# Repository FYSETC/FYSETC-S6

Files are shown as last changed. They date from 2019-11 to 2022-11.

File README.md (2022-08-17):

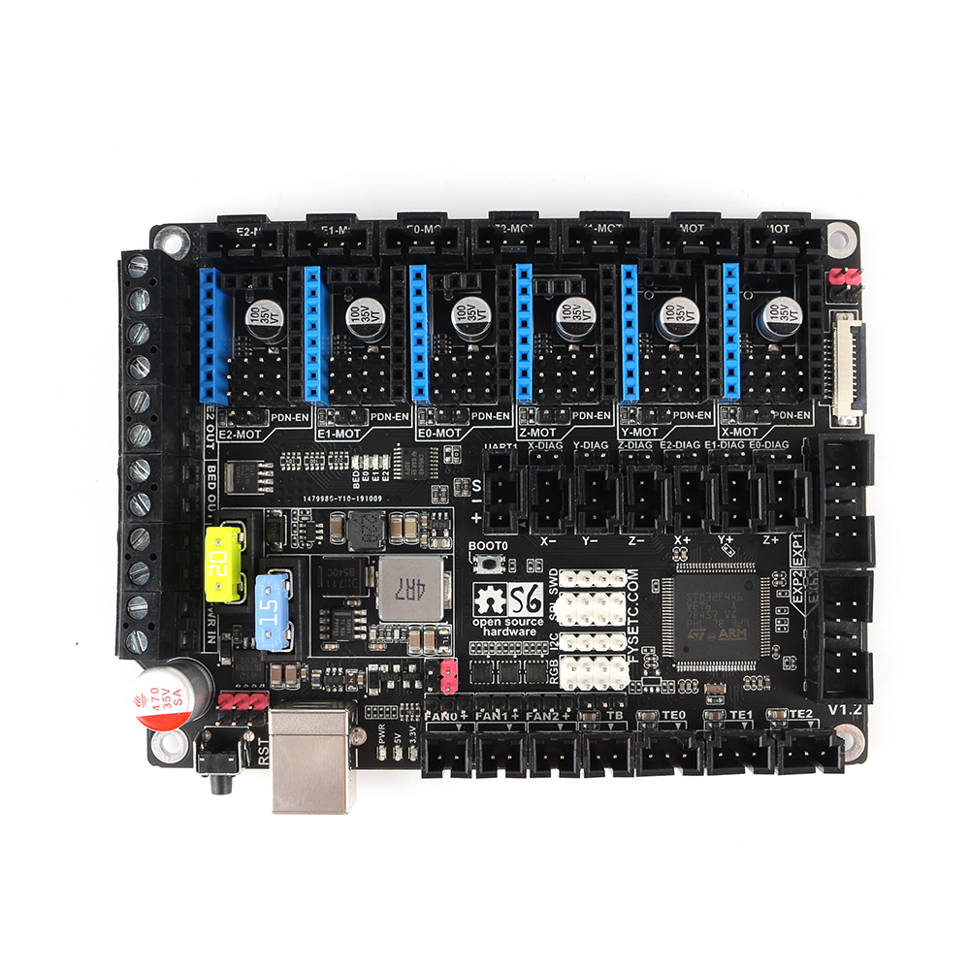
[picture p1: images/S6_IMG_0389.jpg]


The S6 is based on the STM32F446 32bit mcu, like the F6, has six drive sockets and supports the full range of TMC drives. We have fully extended the resources of the MCU so that you can maximize its power. We considered the possible use scenarios of 3D printers and designed a series of extended applications, such as anti-reverse circuit, 12V power supply, thermocouple support, 24V sensor support and so on.

## 1. Features

- Compact size: 117mm x 87mm，Same as F6
- Based on STM32F446 180Mhz，all IOs can withstand 5V voltage
- 6 TMC stepper drivers support, no need wire Uart/SPI
- Improved TMC jumper settings ，simpler and easier to understand
- Main power reverse protection circuit，safer
- 28V input max，12V@5A，5V@2ADC-DC circuit，3.3V@0.6A LDO
- Two car fuses for hot bed input and main power input
- Limit switch socket 24V/5V/3.3V optional, ready for more other equipment, such as -inductive sensor, BL-Touch
- XH connector and MX connector are optional
- 10x PWM capable power mosfet outputs (1 for HotBed, 3 for Heat-End, 3 for fans, 3 for RGB LED strip) 
- 3pin temperature header, you can use thermistor or thermocouple (requires AD597 module)
- 3 ways PWM fans ，2 ways RGB led ，12V & 24V optional
- Easy DISPLAY + SD-CARD connector:

  - RepRapDiscount SmartController compatible pin header on board
  - 10P FPC for Serial Touch display
  - 2X4 PinHeader Out for SD Card moudle 
  - EXP1 & EXP2 have more multiplexing functions, such as USART, I2C, CAN
- SD card & USB upload support
- S6 v2.1: **Add more protection** **(current** **limit resistor, VMOT fuse)**

## 2. Application

---

- 3D printer 

- CNC Device

- Other similar machines

## 3. Hardware 

### 3.1 Reasources

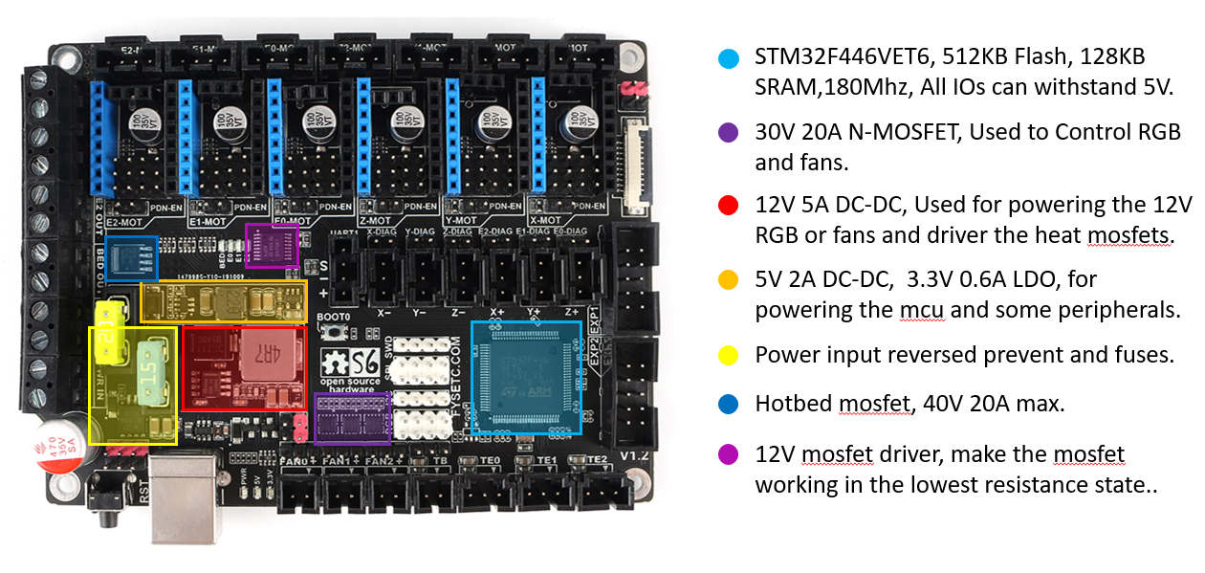
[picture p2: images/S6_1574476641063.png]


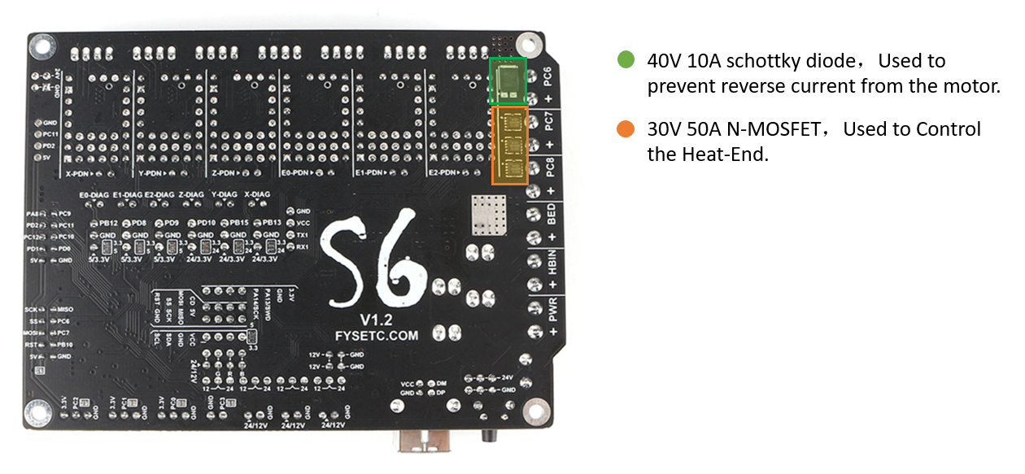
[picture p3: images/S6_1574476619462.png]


| Board Name | S6 | F6 |
| --- | --- | --- |
| License | GPL V2.0 | GPL V2.0 |
| Latest Version | V1.2 | V1.4 |
| Extruders | 3 Max | 3 Max |
| Fixed Fans | 5 Max | 5 Max |
| Controlled Fans | 3 Max | 3 Max |
| Heaters | 3 Max | 3 Max |
| Endstops | 6 Max | 6 Max |
| Temp sens | 4 Max | 4 Max |
| SPI | 2 Max | 1 |
| I2C | 3 Max | 1 |
| ISP | -- | 1 |
| Serial port chip | -- | CH340 |
| CPU | STM32F446VET6 | Atmega2560 |
| CPU Speed ( MHz ) | 180Mhz | 16 Mhz |
| Stepper driver | 6 Max | 6 Max |
| Stepper driver  Type | All StepStick compatible modules | All StepStick compatible modules |
| Input | Main PWR：12-24V 15A Max；BED IN：12-24V 20A Max | Main PWR：12-24V 10A Max；BED IN：12-24V 15A Max |
| Output | BED OUT：20A Max ；Heater Out：5A Max | BED OUT：15A Max ；Heater Out：5A Max |

### 3.2 Jumpers 

---

**Just like the F6 V1.4, the two Z-motor sockets are changed from parallel to series. If you only use one of the sockets, the other must be connected with a jumper cap, otherwise a Z-axis motor will not work.**

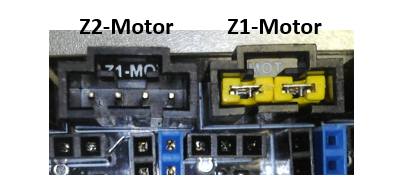
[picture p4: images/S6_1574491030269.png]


#### 3.2.1 Stepper drivers

In order to support as many different drivers as possible, S6 sets a lot of jumper positions. Different drive modules require different jumpers. As shown in the schematic diagram, there are 2 sets of jumpers in the drive section: JP1 and  JP6. 

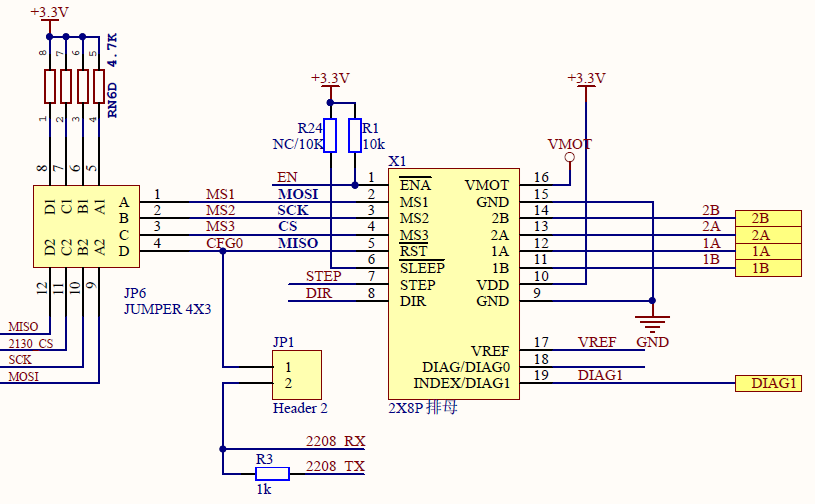
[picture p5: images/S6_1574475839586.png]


In order to give you a better understanding of how to use jumpers for different drivers, I have further illustrated the driver socket. The basic definition of the driver pins is the same, the difference lies in the four places of JP6-1, JP6-2, JP6-3 and JP6-4. You can see their role from the schematic.

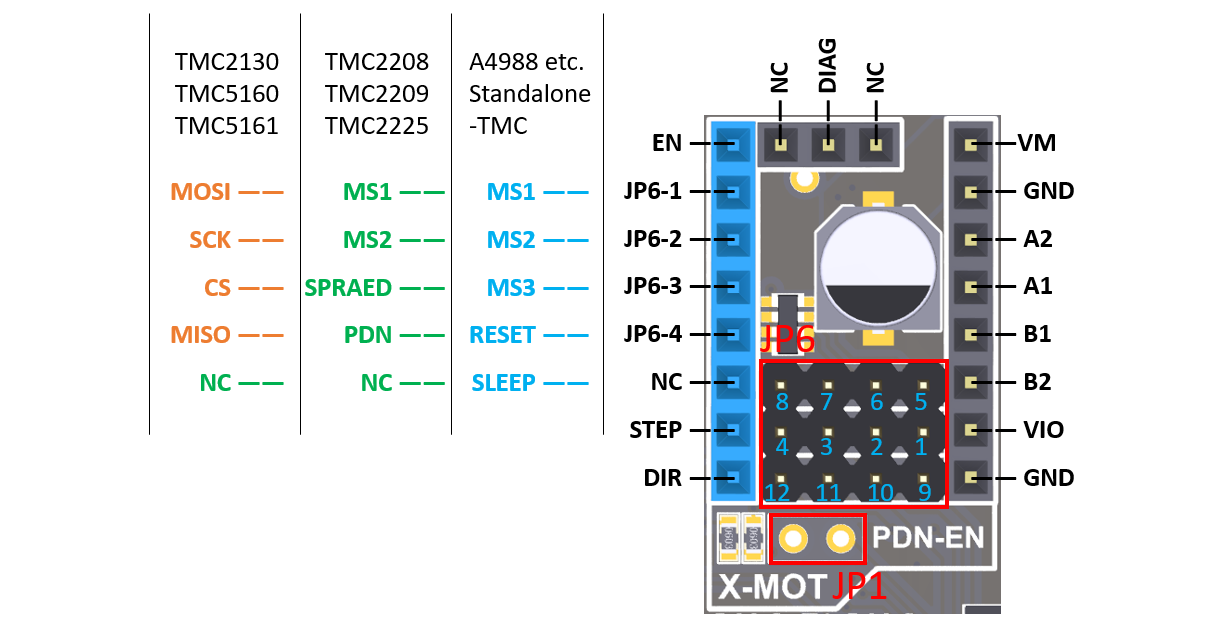
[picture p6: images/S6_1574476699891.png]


##### A4988 jumper config

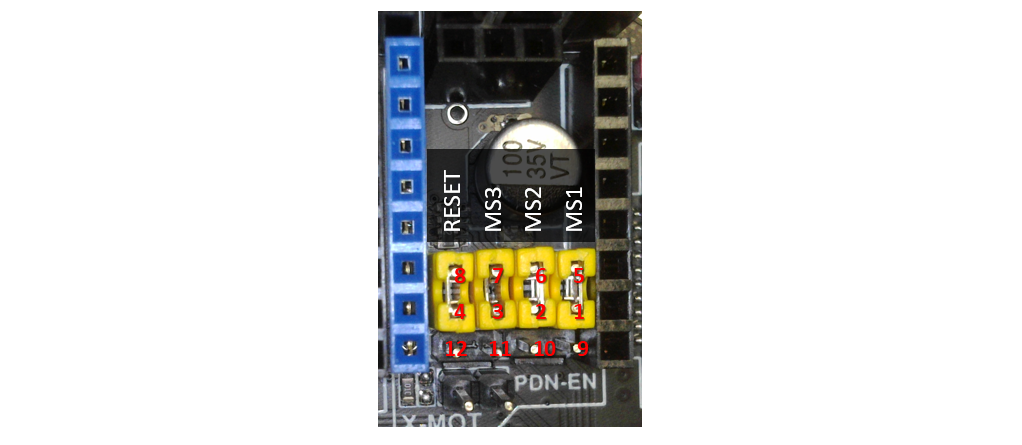
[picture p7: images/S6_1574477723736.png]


- For A4988, A4988 similar, TMC2100 and TMC standalone Mode,  You need jumper JP6 (1234-5678) to config the micro-steps, and some TMC features.
- When you connect the jumper cap, this pin is high. When you are not connected, it is the level state of the module itself. This is different from F6, which can be either high or low.
- For details, please refer to the corresponding driver description.

##### UART mode config

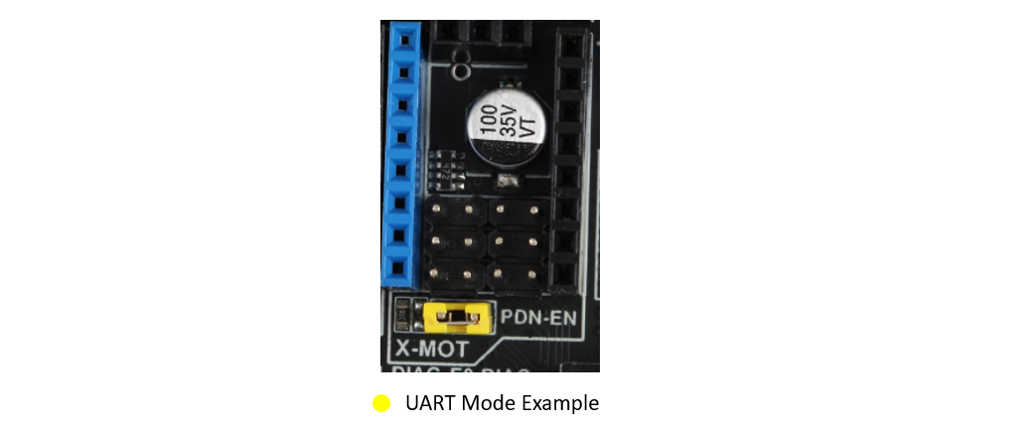
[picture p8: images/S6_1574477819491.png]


- For TMC2208/2225/2209. You just need one jumper to close the JP1, Then the UART mode will enabled.
- You can config all the feature of  the TMC chip via UART, so you can leave all the other jumpers empty.
- Even for 2209, We give 2 lines UART interface to every driver, so no need config the address by MS1/MS2.

###### TMC2209 wiring

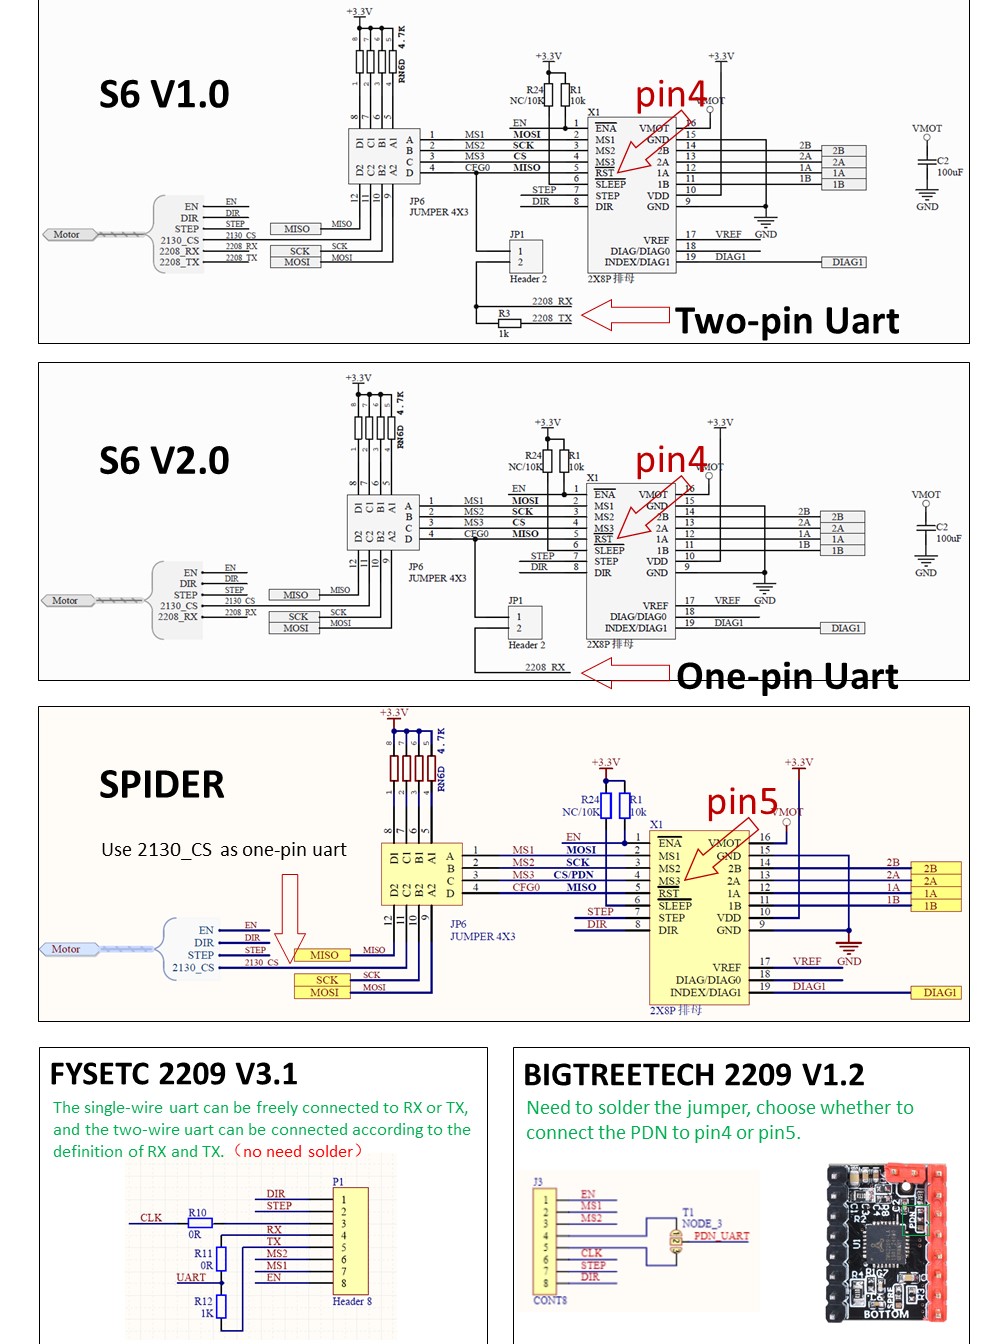
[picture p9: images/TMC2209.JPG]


##### SPI mode config

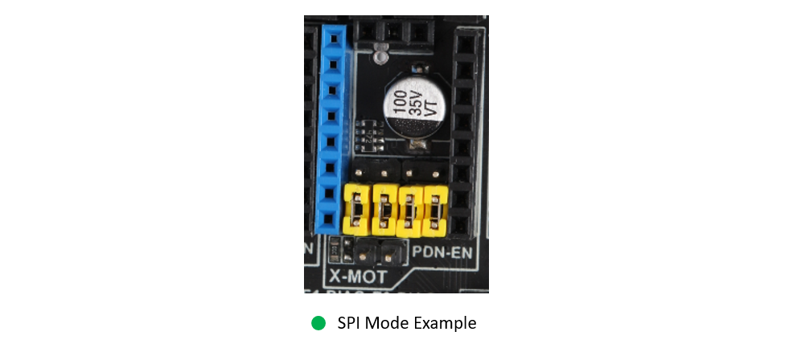
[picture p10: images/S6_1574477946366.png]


- For TMC2130/5160/5161. You need 4 jumpers to close the JP6, Then the SPI mode will enabled.

#### 3.2.2 12V/24V jumpers

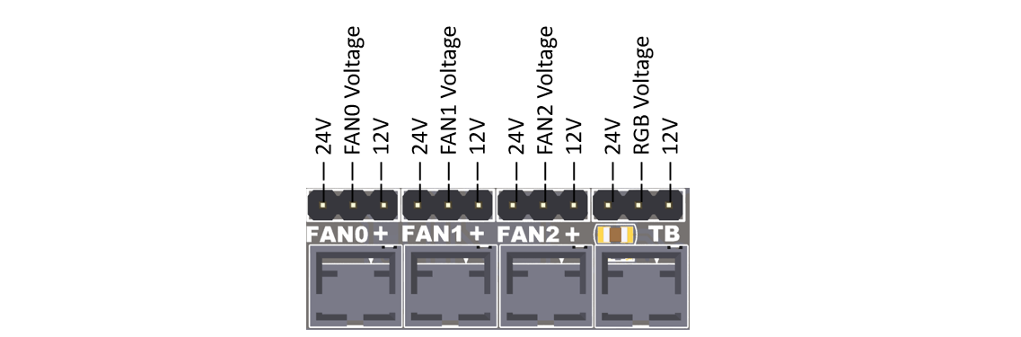
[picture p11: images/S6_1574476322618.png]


- S6 have 12V onboard, Fan and RGB jumpers can refer to this picture and the silk screen at the bottom of the board.
- The input power supply voltage should EXCEED 15v ,if not, the output voltage of 12V DCDC circuit will lower than 12v
- Never let the 12V current exceed 5A, otherwise it will burn out the 12V DCDC circuit.
- If you use an input above 18V, you will get a satisfactory 12V output, otherwise the output may be less than 12V.

#### 3.2.3 DIAG jumpers

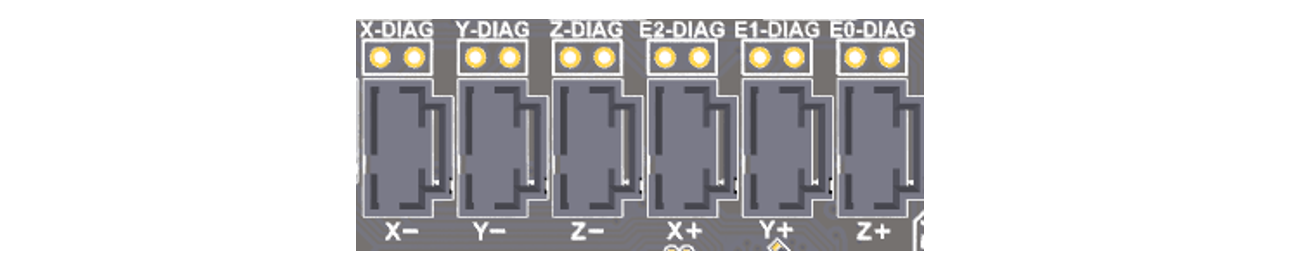
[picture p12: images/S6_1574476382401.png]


- If you use a TMC driver with sensor-less homing(2130/2209/5160/5161), you can connect these jumpers so that the MCU can get the DIAG signal through the corresponding end-stop pin to achieve sensor-less.
- After connect the jumper, remember define the DIAG pins in the firmware and enable the feature.

#### 3.2.4 Bottom jumpers

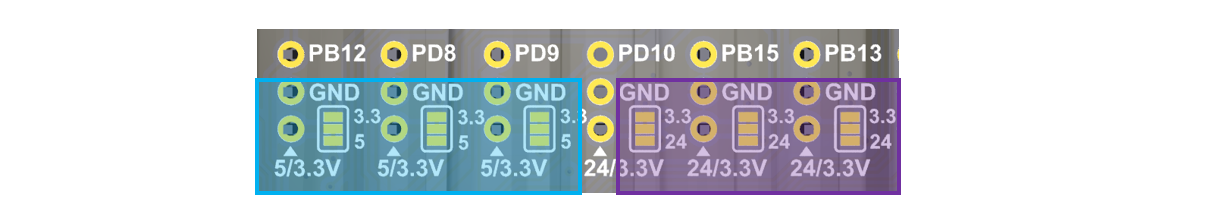
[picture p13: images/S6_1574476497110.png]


- X+ / Y+ / Z+ , You can choose 5V or 3.3V, For X+ & Y+, the default is 3.3V. For Z+, The default is 5V, You can connect BLtouch here.

- X- / Y- / Z- , You can choose 24V or 3.3V, the default is 3.3V. You can switch to 24V, if you want to use some inductive or capacitive sensors.

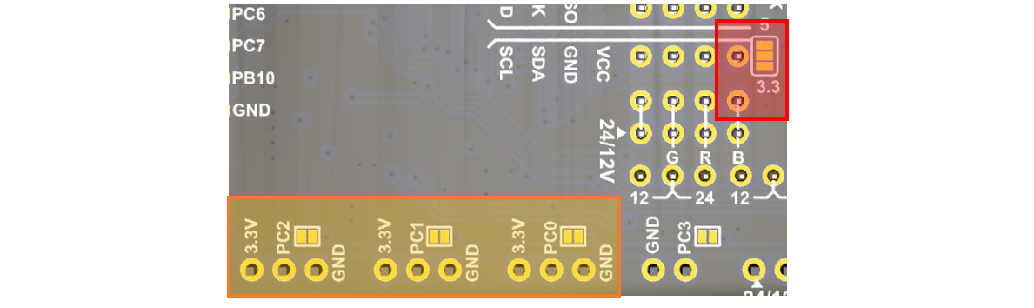
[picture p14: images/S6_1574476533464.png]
  

- I2C pins, You can choose 5V or 3.3V, the default is 3.3V. 

- For TE0-TE2, You can cut the jumper if you want use a thermocouple temperature measurement through AD597.

#### 3.2.5 Jumper for 5V

S6 **V2.0** version adds 5V selection jumper. You can choose 5V from USB or DC circuit. 

Know issue: With 5V USB jumper selected, 24V applied, USB cable disconnected, the heater FETs will turn on.  So we recommend you to choose 5v from DC5V.

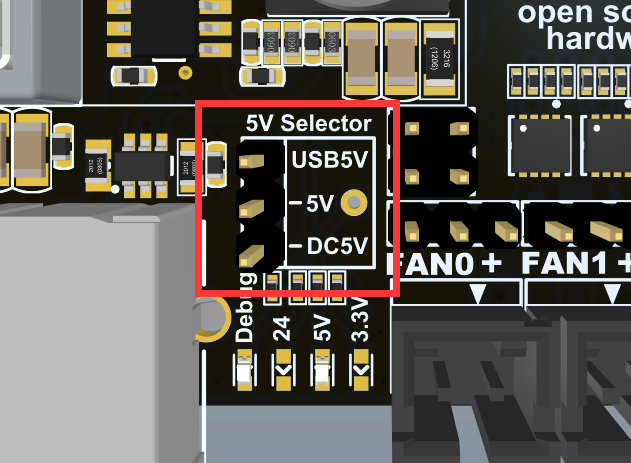
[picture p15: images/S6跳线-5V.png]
S6跳线-5V


#### 3.2.6 Jumper for Boot0

In S6 V2.0, the BOOT0 button is replaced by a jumper.

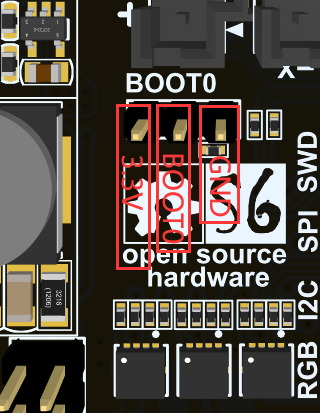
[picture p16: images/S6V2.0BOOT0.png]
S6V2.0BOOT0


### 3.3 Pin Definition

All the pins we have marked on the back of the board, if you need to, you can confirm the board in reverse or check the sch.

Thanks to the power of the STM32, each pin has multiple functions, I will identify it for your reference as much as possible. For further information, please refer to the STM32F446 datasheet, which I have placed on our [S6 GitHub](https://github.com/FYSETC/FYSETC-S6/blob/master/datasheet/stm32f446ve.pdf)

#### 3.3.1 EXP1&EXP2

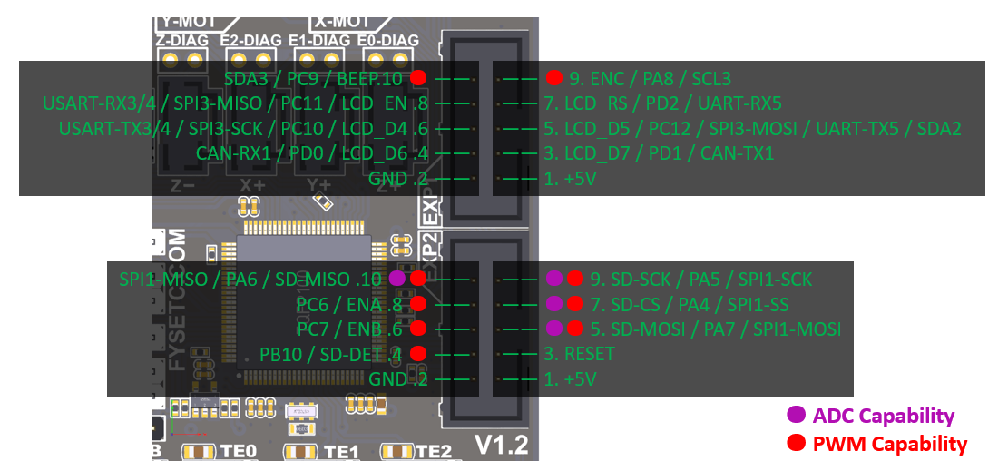
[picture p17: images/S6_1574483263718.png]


#### 3.3.2 Eedstops and UART1 Pins

The UART socket next to the limit switch can be used to connect serial devices such as the wifi module, or to update the firmware through the serial port.

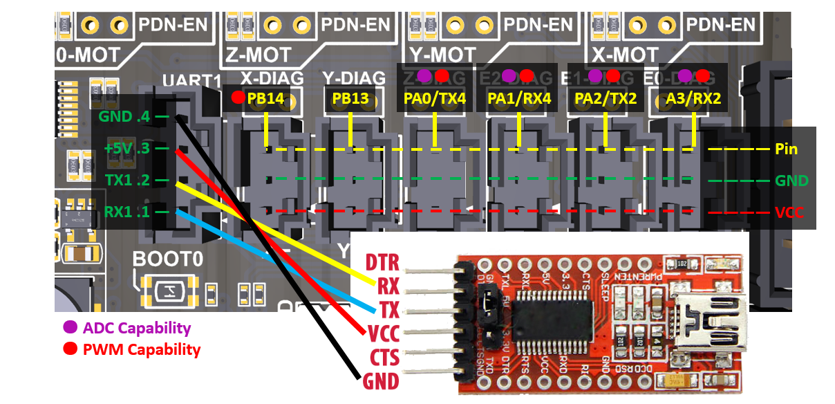
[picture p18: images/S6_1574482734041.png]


#### 3.3.3 BL-touch Wiring Example

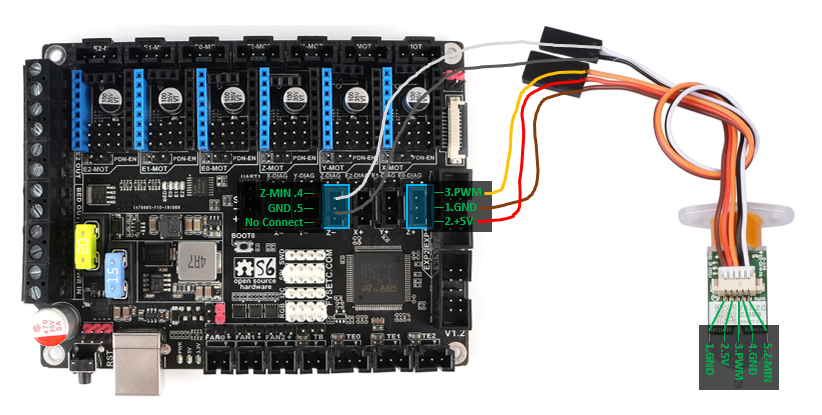
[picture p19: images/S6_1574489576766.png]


#### 3.3.4 Reuse RGB ports for FAN

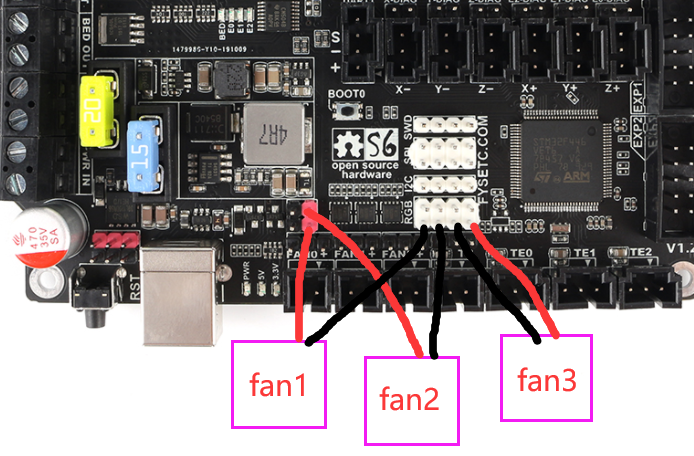
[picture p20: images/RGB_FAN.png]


## 4. Firmware

---

### 4.1 Marlin

#### 4.1.1 Download Vscode + platformio

To compile the firmware , you need to install Visual Studio Code and the platformio pulg-in. More details of Marlin build, check [here](https://marlinfw.org/docs/basics/auto_build_marlin.html).

#### 4.1.2 Download firmware

##### S6 v1.2

The firmware is in the `firmware` folder in this repository, and if you want to know what we have changed , we recommend to use git to get the code .

If you want to have latest feature of Marlin , we recommend to use latest [Marlin bugfix-2.0.x branch](https://github.com/MarlinFirmware/Marlin/tree/bugfix-2.0.x) , after downloading ,you need to enable following define in ```configuration.h``` file  

```#define MOTHERBOARD BOARD_FYSETC_S6```

then change the ```default_envs``` variant in ```platformio.ini``` file

```default_envs = FYSETC_S6_8000``` (Recommended. boot address is `0x8000`. You need to flash the bootloader([github](https://github.com/FYSETC/FYSETC-S6/blob/main/bootloader/Bootloader-FYSETC_S6.hex) [gitee](https://gitee.com/fysetc-mirrors/FYSETC-S6/blob/main/bootloader/Bootloader-FYSETC_S6.hex)) first, check the `README` on the link)

```default_envs = FYSETC_S6``` (For old bootloader,boot address is `0x10000`, you need to flash this bootloader([github](https://github.com/FYSETC/FYSETC-S6/blob/main/bootloader/Bootloader-FYSETC_S6_10000.hex) [gitee](https://gitee.com/fysetc-mirrors/FYSETC-S6/blob/main/bootloader/Bootloader-FYSETC_S6_10000.hex)) first , check the `README` on the link)

**Note: The bootloader boot address have been change to `0x8000` since 2021/06/23, you can check bootloader details [here](https://github.com/FYSETC/FYSETC-S6/tree/main/bootloader), and you can check the Marlin PR [here](https://github.com/MarlinFirmware/Marlin/pull/22207).**

##### S6 v2.x

The firmware is in the `firmware` folder in this repository , you can also get the firmware from latest [Marlin bugfix-2.0.x branch](https://github.com/MarlinFirmware/Marlin/tree/bugfix-2.0.x). You need to enable following define in ```configuration.h``` file  

```#define MOTHERBOARD BOARD_FYSETC_S6_V2_0```

then change the ```default_envs``` variant in ```platformio.ini``` file

```default_envs = FYSETC_S6_8000``` (Recommended. boot address is `0x8000`. You need to flash the bootloader([github](https://github.com/FYSETC/FYSETC-S6/blob/main/bootloader/Bootloader-FYSETC_S6.hex) [gitee](https://gitee.com/fysetc-mirrors/FYSETC-S6/blob/main/bootloader/Bootloader-FYSETC_S6.hex)) first, check the `README` on the link)

```default_envs = FYSETC_S6``` (For old bootloader,boot address is `0x10000`, you need to flash this bootloader([github](https://github.com/FYSETC/FYSETC-S6/blob/main/bootloader/Bootloader-FYSETC_S6_10000.hex) [gitee](https://gitee.com/fysetc-mirrors/FYSETC-S6/blob/main/bootloader/Bootloader-FYSETC_S6_10000.hex)) first , check the `README` on the link)

**Note: The bootloader boot address have been change to `0x8000` since 2021/06/23, you can check bootloader details [here](https://github.com/FYSETC/FYSETC-S6/tree/main/bootloader), and you can check the Marlin PR [here](https://github.com/MarlinFirmware/Marlin/pull/22207).**

#### Compile the firmware

Open Vscode and open platformio main page and click the "Open Project" button , and direct to the folder where you put your firmware.

![1561099422559](images/AIO_f1.png)

If everything goes fine , at the bottom you can see several buttons

![1561099546202](images/AIO_f2.png)

The check mark is for compiling , click it to compile.

If you generate the hex file fail you may need to open vscode using Administrator Account .

### 4.2 Klipper

You need to follow the Klipper [installation guide](https://www.klipper3d.org/Installation.html) to install [Klipper](https://github.com/KevinOConnor/klipper).

When calling `make menuconfig`, please select below options

#### 4.2.1 menuconfig

- #### Enable `extra low-level configuration options`

- #### Micro-controller Architecture

Select `STMicroelectronics STM32`

- #### Processor model

Select `STM32F446`

- #### Clock reference

Select `12 MHz crystal`

- #### Bootloader offset

- ##### 1. Boot address no

If you choose `No bootloader` bootloader offset in Klipper `make menuconfig`, then you use DFU([method1](#jump4) [method2](#jump)) to upload the firmware to S6 board. **But you need to set the 'Start address' to `0x08000000`**. 

![image-20210705151440643](images/menuconfig1.png)

- ##### 2. Boot address 32k

If you choose `32k` bootloader offset in Klipper `make menuconfig`. Then you need to flash the S6 board bootloader named `Bootloader_FYSETC_S6` first (If you get your S6 board after `2021/06/23`, no worries, the bootloader is on the board when it leave the factory). The bootloader is in the folder named `bootloader` in this repo, please follow the README in bootloader folder([github](https://github.com/FYSETC/FYSETC-S6/tree/main/bootloader) or [gitee](https://gitee.com/fysetc/FYSETC-S6/tree/main/bootloader)). Then you can follow [Upload the firmware(SDCARD)](#jump1) to flash your built Klipper firmware to S6. Or you can use DFU([method1](#jump4) [method2](#jump)) to upload your firmware, but **remember to change flash address to `0x08008000`** with these two methods. 

![image-20210705151337765](images/menuconfig2.png)

- ##### 3. Boot address 64k

If you choose `64k` bootloader offset in Klipper `make menuconfig`. Then you need to flash the S6 board bootloader named `Bootloader_FYSETC_S6_10000` first. The bootloader is in the folder named `bootloader` in this repo, please follow the README in bootloader folder([github](https://github.com/FYSETC/FYSETC-S6/tree/main/bootloader) or [gitee](https://gitee.com/fysetc/FYSETC-S6/tree/main/bootloader)). Then you can follow [Upload the firmware(SDCARD)](#jump1) to flash your built Klipper firmware to S6. Or you can use DFU([method1](#jump4) [method2](#jump)) to upload your firmware, but **remember to change flash address to `0x08010000`** with these two methods. 

![image-20210705151951142](images/menuconfig3.png)

#### 4.2.2 Compile firmware

```
make
```

#### 4.2.3 Upload firmware

Follow Firmware Update guide [here](#jump0).

### 4.3 Upload firmware

#### 4.3.1 Upload the firmware(SDCARD)

We provide several ways to upload the firmware .Uploading with SD card is our default way to update the firmware as the board already has the sdcard bootloader in it when it leave the factory. If you choose to upload the firmware with a sdcard. First you need to connect a sdcard module to the S6 EXP2 port. Basically , you can use any kind of LCD screen(like our [mini12864](https://github.com/FYSETC/FYSETC-Mini-12864-Panel)) that contain sdcard module. But if you can't make it work , check if your sdcard module's SPI CS pin connected to PA4 pin in S6 board.

Then,copy your compiled firmware file ```firmware.bin``` file to the SD card , and insert it to the SD card module , and then power on the board. You may need to wait for about 30s to finish uploading. 

Note: The bootloader is in the folder named `bootloader`, please follow the README in [bootloader folder](https://github.com/FYSETC/FYSETC-S6/tree/main/bootloader).

#### 4.3.2 <span id="jump4">Upload the firmware(dfu-util)</span>

This method works in linux, that means should work in raspberry pi.

1. Enter DFU mode first

   - First power off the board
   - Set jumper on 5v pin and DC5V ![](images/5vJumper.png)
   - Place jumper on BT0 to 3.3V pin ![](images/boot.png)
   - Connect USB cable to the board and your computer 
   - Power up the board with 24v 

2. Make sure dfu-util is installed, shoot `dfu-util --version` command to check.

   Sample output:

   ```
   dfu-util 0.9
   
   Copyright 2005-2009 Weston Schmidt, Harald Welte and OpenMoko Inc.
   Copyright 2010-2016 Tormod Volden and Stefan Schmidt
   This program is Free Software and has ABSOLUTELY NO WARRANTY
   Please report bugs to http://sourceforge.net/p/dfu-util/tickets/
   ```

   If not , you should install it first, use the package manager of your distribution to get the latest version, like

   ```
   sudo apt-get install dfu-util
   ```

3. Then use the command below to upload the firmware. You should replace `firmware.bin` below with your built firmware bin file location like `out/klipper.bin` if you use klipper firmware. Change flash address `0x08008000` to bootloader you choosed. (If you use Marlin and your platformio env is `default_envs = FYSETC_S6`, then you need to set it to `0x08010000` and you need bootloader , if you use klipper firmware and you choose boot address `32kiB bootloader` when compiling klipper then set it `0x08008000`, if `64kiB bootloader` , set it `0x08010000`. if `no bootloader` set it to `0x08000000`)

   ```
   dfu-util -R -a 0 -s 0x08008000:leave -D firmware.bin
   ```

#### 4.3.3 <span id="jump">Upload the firmware(DFU)</span>

The other way to upload the firmware is using DFU. 

##### Step 1. Download stm32cubeprogrammer 

You can download it from ST website.

https://www.st.com/zh/development-tools/stm32cubeprog.html

Open the STM32CubeProgrammer software.

![1574332767079](images/S6_1574332767079.png)

##### Step 2. Enter DFU mode

S6 v1.2

First power off the board , then push the Boot0 button and hold it , then connect the USB to the board and your computer , it will enter DFU mode . Now you can loose you hand from Boot0 button.

S6 v2.x

First power off the board , then jumper the Boot0 to 3.3V , then connect the USB to the board and your computer , it will enter DFU mode . 

***REMEMBER to remove the jumper if you finish uploading or it will enter DFU mode again.***

##### Step 3. Upload the firmware

Now you can connect and flash the S6 board with stm32cubeprogrammer with the following operation.

![1574386395071](images/S6_1574386395071.png)

Do as the red number shows in the screen shot.

1. Click the button to flesh the DFU port.

2. Connect the DFU 

3. Choose the "firmware.bin" file.

4. fill in the 'Start address' with `0x8008000` (If you use Marlin firmware and your platformio env is `default_envs = FYSETC_S6`, then you need to set it to `0x08010000`, if env is `default_envs = FYSETC_S6_8000`, then you need to set it to `0x08008000` . If you use klipper firmware and you choose boot address `32kiB bootloader` when compiling klipper then set it `0x08008000`, if `64kiB bootloader` , set it `0x08010000`. if `no bootloader` set it to `0x08000000`)

5. Start Programming

**We will continue to update, please look forward to it!**

## 5. Tech Support

You can submit issue in our github https://github.com/FYSETC/FYSETC-S6/issues
Or submit any technical issue into our [forum](http://forum.fysetc.com/) 

## 6. Related Articles

[English](https://3dwork.io/en/fysetc-s6-complete-guide/)

[Español](https://3dwork.io/fysetc-s6-guia-completa/)

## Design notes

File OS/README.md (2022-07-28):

# OS

## SAMFi-OS_OrangePi_zero

Before you config the [SAMF-OS_OrangePi_zero](https://github.com/FYSETC/FYSETC-SAMFi-OS). You need an TF card with at least 8G capacity.

### Step 1

Download and flash the OS image with `balenaEtcher` software to your TF card. Insert your flashed TF card to OrangePi-zero and connect Ethernet cable then power on. Find the ip address of OrangePi-zero on your router, host name is `orangepizero`.

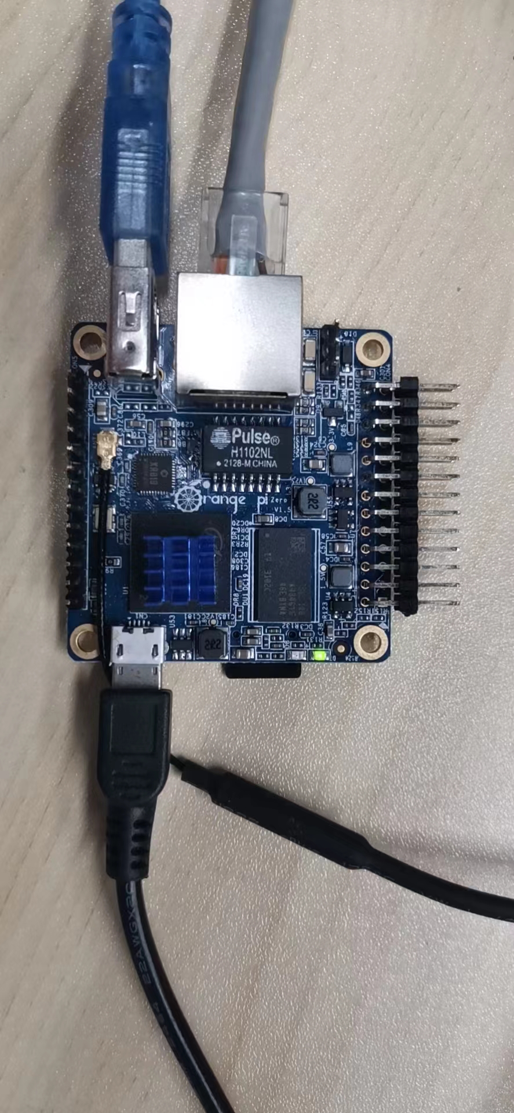
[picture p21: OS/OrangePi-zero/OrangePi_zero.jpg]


### Step 2

You can find the firmware `klipper.bin` in `OrangePi-zero` folder after you download the github repository. It is also stay in the OS path `firmwares\s6.bin` after you login the OS with SSH.

Original SSH account and password:

```
account: fysetc
password: fysetc123
```

Enter DFU mode(set a jumper on `3.3V` and `BOOT0` pin and re-power on the board ), and flash the firmware with the command below after you connect your OrangePi and S6 with USB cable.

```
dfu-util -R -a 0 -s 0x08008000:leave -D firmwares/s6.bin
```

or follow the instructions [here](https://github.com/FYSETC/FYSETC-SPIDER#44--firmware-upload) for firmware uploading. 

Remember to remove the `3.3v` `BOOT0` jumper and click the reset button after you flashed the firmware. 

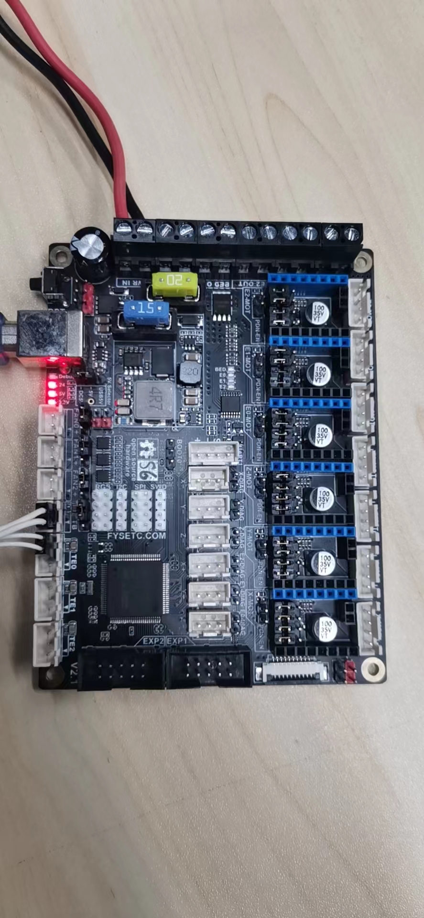
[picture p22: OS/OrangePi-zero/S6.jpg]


### Step 3:

Prepare the `pinter.cfg`, using the command below

```
cp klipper_config/s6-v2.cfg klipper_config/printer.cfg
```

You probably need to change `id` by `ls /dev/serial/by-id` command.

I use the generic config for this example, you need to change the config according to your machine. Now visit the webpage with your orangepi-zero IP address. Good to go.

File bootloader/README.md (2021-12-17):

## Bootloader

**First of all, you need know that, the FYSETC S6 bootloader boot address have been change to `0x8000` since 2021/06/23. So the default bootloader `Bootloader-FYSETC_S6.hex` boot address is `0x8000`. And the old bootloader boot address is `0x10000`, and the repo still contains it, its name is  `Bootloader-FYSETC_S6_10000`. So when you are going to update the bootloader, you should choose the right one.** 

#### Upload the bootloader(DFU)

##### Download stm32cubeprogrammer 

You can download it from ST website.

https://www.st.com/zh/development-tools/stm32cubeprog.html

Open the STM32CubeProgrammer software.

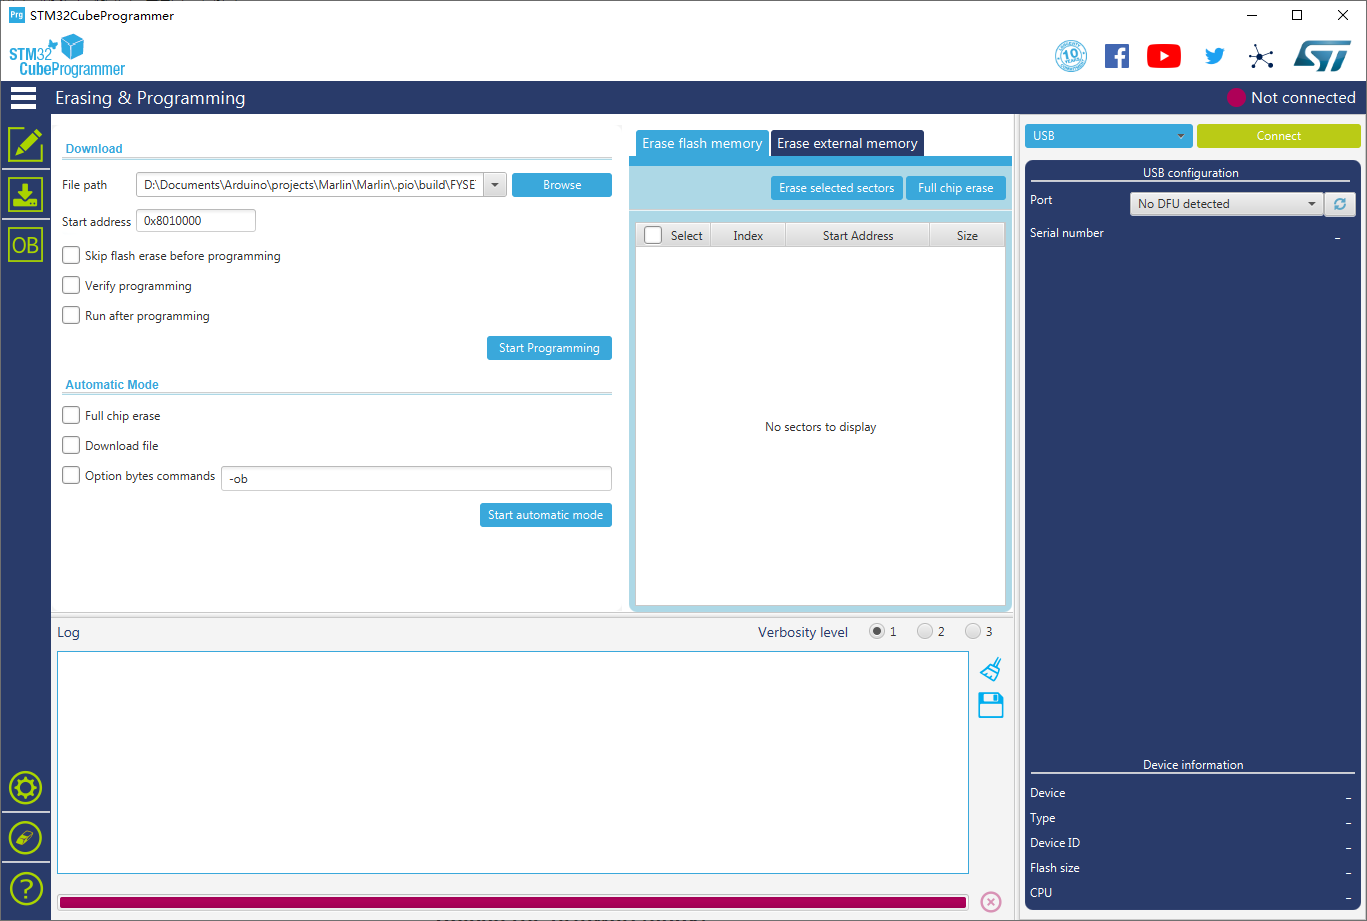
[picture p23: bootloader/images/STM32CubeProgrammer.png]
STM32CubeProgrammer


##### Enter DFU mode

S6 v1.2

First power off the board , then push the Boot0 button and hold it , then connect the USB to the board and your computer , it will enter DFU mode . Now you can loose you hand from Boot0 button.

S6 v2.0

First power off the board , then jumper the Boot0 to 3.3v, then connect the USB to the board and your computer , it will enter DFU mode . 

***REMEMBER to remove the jumper if you finish uploading or it will enter DFU mode again.***

##### Upload the bootloader

Now you can connect and flash the S6 board with STM32CubeProgrammer with the following operation.

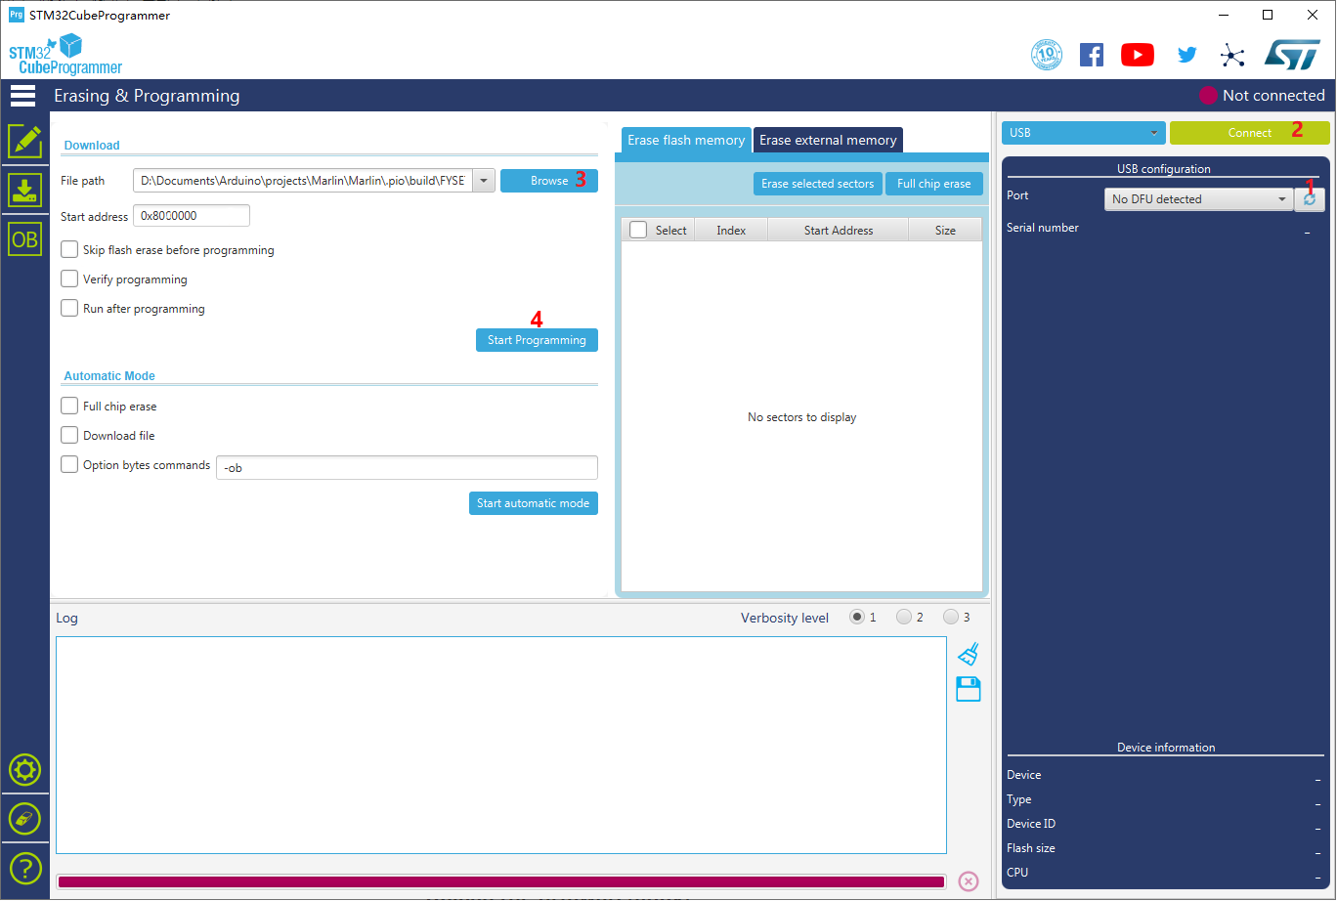
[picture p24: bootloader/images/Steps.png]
Steps


Do as the red number shows in the screen shot.

1. Click the button to flesh the DFU port.

2. Connect the DFU 

3. Choose the downloaded "Bootloader-FYSETC_S6.hex" file (If old bootloader, see below, choose `Bootloader-FYSETC_S6_10000`). 

6. Start Programming

**We will continue to update, please look forward to it!***

**You need know that, the FYSETC S6 bootloader boot address have been change to `0x8000` since 2021/06/23. So the default bootloader `Bootloader-FYSETC_S6.hex` boot address is `0x8000`. And the old bootloader boot address is `0x10000`, and the repo still contains it, its name is  `Bootloader-FYSETC_S6_10000`. So when you are going to update the bootloader, you should choose the right one.** 

## Tech Support
You can raise issue in our github https://github.com/FYSETC/FYSETC-S6/issues
Or submit any technical issue into our [forum](http://forum.fysetc.com/)

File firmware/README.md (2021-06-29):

# Firmware

The Marlin default configurations are below:

```
#define BAUDRATE 115200
#define MOTHERBOARD BOARD_FYSETC_S6_V2_0
#define SDSUPPORT
#define TOUCH_UI_FTDI_EVE
```

You need to change configurations for you own machine. 

# Pre-builds

If you use `Marlin-0x8000.bin` then you need the bootloader `Bootloader-FYSETC_S6.hex`. And if you use `Marlin-0x10000.bin`, you need bootloader named `Bootloader-FYSETC_S6_10000.hex`. You can get the bootloader [here](https://github.com/FYSETC/FYSETC-S6/tree/main/bootloader).

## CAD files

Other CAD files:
hardware/V1.2/S6 V1.2.DWG

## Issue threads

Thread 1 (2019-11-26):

Silkscreen wrong?

Drachenkaetzchen, 2019-11-26:
Hi,

I received my Fysetc S6 1.2 today and noticed that the silkscreen designators do not match the schematic. For example, on my board Z+ is labeled with PB12 but the schematic says Z+ is PA3. Is this an error on the silkscreen or does my board have a different pinout?

Thanks
Felicia

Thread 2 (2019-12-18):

Limit switch protection?

vallentinc, 2019-12-18:
Hello.
A defective endstop and/or a probe can feed voltage (let's say 24V) directly into the STM32, burning it. There is no diode or current limiting device on the endstops.
Any idea why?

Hermiedaddy2, 2021-12-22:
I noticed this too.  The creality end stops have a small pcb with diode, resistor and capacitors.  Unless you use that kind of endstop I would only select 3.3v on the underside for the endstops.

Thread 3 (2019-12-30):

flashing from SD card

aleknest, 2019-12-30:
- connect SD card module and see content (m20 g-code)
- place firmware.bin to SD card, power on and nothing. I  see previous firmware

GerogeFu, 2019-12-31:
The bootloader prefer low speed SD cards. Change to low speed sdcard if you have. If not , use the other way to upload the firmware .

ModestAndroid, 2020-01-02:
I grabbed an old 2GB SD card, formatted it to FAT, and was able to flash the firmware. Glad I found this thread!

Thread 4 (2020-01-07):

Cannot compile a working firmware with TMC_DEBUG enabled

dbemowsk, 2020-01-07:
I am running the S6 board with the Fysetc TMC2209 drivers and every time I enable TMC_DEBUG in configuration_adv.h and upload the firmware to the board, I do not get serial communication from the USB port after rebooting from a firmware upload.  With this disabled I don't get the full diagnostic information when sending an M122 command.  I have posted this problem in multiple places (Fysetc forum, contact form on their website and tried to join their facebook group) and have not received any response from Fysetc tech support from ANY of my posts.  SO now I will try here.

dbemowsk, 2020-01-07:
OK, so I did a test.  In STM32CubeProgrammer there is a checkbox to "run after programming".  I compiled the firmware with TMC_DEBUG enabled and uploaded it to the board with that checked.  Once the upload finishes, DFU disconnects and the computer sees the serial port in device manager.  I connect with a terminal and I can send the M122 command and get the full stats from the drivers.  That's all I tried, but I am sure I could send any valid Gcode and it would probably run just fine.  BUT, the minute I press the reset button or disconnect and reconnect the USB cable, the serial port is lost and not detected again by Windows.  So, I am just making an assumption here that the action of pushing the reset button or plugging in the USB cable is supposed to execute the firmware code, but it doesn't do that when TMC_DEBUG is enabled in the firmware.  That ONLY works if TMC_DEBUG is disabled in the firmware.  I hope that gives someone a clue as to what is going on.

dbemowsk, 2020-01-07:
I ended up finding that the bootloader was corrupted on the board.  After flashing the bootloader again, everything worked.  The part that was confusing an didn't make me think of the bootloader at first was the fact that if I disabled TMC_DEBUG and uploaded, it would appear to work normally.  After uploading the bootloader though all TMC_DEBUG functions worked.

MarkV3082, 2022-04-02:
> I ended up finding that the bootloader was corrupted on the board. After flashing the bootloader again, everything worked. The part that was confusing an didn't make me think of the bootloader at first was the fact that if I disabled TMC_DEBUG and uploaded, it would appear to work normally. After uploading the bootloader though all TMC_DEBUG functions worked.

How did you get the Bootloader to successfully upload to the Board. I have tried using STM32 programmer but I get a can't compile message "Found " when it expected a Hex character on Line 31

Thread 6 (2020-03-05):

Pwm Fan issue

andysport, 2020-03-05:
So, today I have installed a S6 board on my ender 3.  Drivers, endstops, stepper motors, bed and hotend work find, but I have a strange behavior when I power on pwm layer fan. Infact in FAN0 connector it run always at 100% of speed. If I connect the fan on FAN1, it is always off. At last, if I connect the fan FAN2, finally it works as aspect ( pwm mode).
I want to specify that the hotend is connect to E0 24V connector, and the thermistor is connected on TE0 connector.
Could anyone explain me this behavior, or help me to resolve this?
Thanks

GerogeFu, 2020-03-06:
Try this branch https://github.com/FYSETC/Marlin-2.0.x-FYSETC/tree/S6/2.0.x

andysport, 2020-03-06:
I tried to compile many times but I have an error when VS create firmware.elf
The error is showed in the picture.
I specify that there are no warning or errors when I compile the firmware
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

andysport, 2020-03-06:
I tried to compile many times but I have an error when VS create firmware.elf
The error is showed in the picture.
I specify that there are no warning or errors when I compile the firmware.
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

GerogeFu, 2020-03-06:
Is the .bin file created ?

andysport, 2020-03-06:
Unfurtunately no .bin is created, I 'll compile the firmware with administrator  account.
However I had no problem if use vanilla Marlin version.

GerogeFu, 2020-03-06:
I test again , if you just download the branch and change nothing , it can be compiled.

andysport, 2020-03-06:
Ok. I made some change because I have, ender 3 lcd, tmc2130 driver ( spi), manual bed levelling, adaptive smoothing, s_curve acceleration. I compile the firmware with cr10 stocklcd voice in configuration.h

andysport, 2020-03-09:
So, finally I have compiled the firmware and I test it as download and with my configuration. Both the firmware have the same behavior and the issue describe before it's always present

GerogeFu, 2020-03-10:
I tested the fan again. It works. Check your fan voltage selection . You can choose 12V or 24V for your fan with a jumper.  Test the fan using command "M106 S255" to turn on the fan and "M106 S0" to turn off the fan.

andysport, 2020-03-10:
So, thanks for your support. Few minute ago I did some test and as you say the FAN 1 and 2 work as aspect but for fan 1 there is a bug in marlin because if I want to turn on the fan 1 with lcd when I press on the Fan 2 voice in temperature menù, the system show me the Fan 3. I think that's is a bug.
For FUN 0 I think there is something broken because it works always at 100 % speed. How I can verify this?

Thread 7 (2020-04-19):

SPI port AUX-3

kunpoolsion, 2020-04-19:
Hello,
I wanna add a MAX7219 led matrix to the SPI port close to RGB pins.
Can´t find in definition or scheme what are the corresponding pins in mcu or if those pins are share with other devices.
Can you clarify it?
I´m not gonna use SPI steppers, but I´m using sd reader at exp2.
Thanks

kunpoolsion, 2020-04-19:
Answering myself, it shares pins with EXP1, so basically, can't have a SD card reader on EXP1 and the led matrix at AUX-3

kunpoolsion, 2020-04-19:
There are any other SPI port that can be use?
If yes, what are the corresponding pins for it?

GerogeFu, 2020-09-19:
Sorry , i don't think there are extra pins. This is a little bit old date question , i going to close it , thanks.

Closed 2020-09-19.

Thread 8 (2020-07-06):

5V Voltage Issue

jdlongenecker, 2020-07-06:
Hello,

I have FYSETC S6 powered by 24V DC Power Supply. Measuring +5V and GND from UART Pin, it reads 4.95-5.0V as expected. However, when I connect Raspberry Pi to USB plug, +5V changes to 4.3-4.4V. This makes my PT100 amplifier inaccurate as it needs 0V and 5V inputs, not 0V and 4.3V input.

If the control board could use internal 5V2A supply even when USB device is connected, it would work better.

GerogeFu, 2020-09-18:
This has been fix in the new version, thanks for report.

dinamitemic, 2020-09-28:
@GerogeFu Same issue here. Also, if I put the tape on the cable in order to do not share the 5V it is not detected anymore. I think it's missing the pullup.
How we can solve this?

Closed 2020-09-18.

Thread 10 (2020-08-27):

I2C devices not working ...

kbahey, 2020-08-27:
I am using the S6 board for a telescope project (OnStep).
It works, and controls the scope as expected.

The issue is that connecting I2C devices (e.g. BME280 for ambient temperature, pressure and humidity) does not work at all.

GerogeFu, 2020-09-18:
If you are using the EEPROM I2C port for you telescope, you need to take care of the extra circuit of this port, you can look into the schematic.

kbahey, 2020-09-18:
The issue is that connecting any I2C device to the I2C pins on the S6 does not work.
We tried the BME280 as an example, with proper VCC and GND to it.
It does not work.

Many people tried, and no one succeeded.

GerogeFu, 2020-09-19:
This IIC circuit is originally for EEPROM , there are extra resistor/cap in the circuit , maybe you need to avoid them
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

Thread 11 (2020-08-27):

Cannot force DFU mode with GPS powered up

kbahey, 2020-08-27:
I am using the S6 board for a telescope project (OnStep).
It works normally for most functions.

However, when having the GPS connected, the board would not enter DFU mode when the BOOT0 button is pressed, then USB cable is inserted.

If I disconnect the 5V going to the GPS, then DFU mode works normally.

Any idea how to solve this?

GerogeFu, 2020-09-18:
I think your power for the GPS goes to back to S6 , so you can power the GPS with S6 but not extra power supply.

kbahey, 2020-09-23:
Can you explain your reply? I don't understand it.

GerogeFu, 2020-09-24:
Oh , ok . I mean your GPS module is feeding the S6 board. But what we need is  S6 board feeding the GPS.

kbahey, 2020-09-24:
No.
The GPS module does not provide power to the S6 board.
It takes power from the board.
And the board takes power from the USB cable.

When I use 12V input to the board, and then press the Boot0, then the Reset button, the board sometimes goes into DFU mode, but sometimes it does. Better than USB only, but not consistent.

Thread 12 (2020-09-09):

[HINT] Problem with TMC and missing vmot

GMagician, 2020-09-09:
I know that 2.0 board is on development and I know that some TMC drivers have a lot of issues (they die) when vmot is missing but vin is present. To solve this issue it's a common way to use vin with a diode to power vmot.

I don't know if 2.0 may be powered (via usb?) with no 12/24V. In such case TMC lose their cnf and requires a reset + reprogram when 12v/24v is given (I noticed this acting at reverse, tmc fully programmed and removed 24V, once 24V comes back tmc 2209 registers are wrong).

There  are some issues reported in Marlin about this weird behavior. On a different test board (ramps) I solved this powering TMC vmot with 5V + diode. It seems that 5v instead of 3.3 solve the issue.

Since I'm looking for 2.0 board it would be a good thing if it may solve such issue

Thanks for your attention

GerogeFu, 2020-09-18:
Thanks very much for this report. I will discuss this with the team. Thanks.

GerogeFu, 2020-09-19:
Discussed with the team, our 2.0 is going to market, so the board is unchangeable, we will try to fix it in 2.1 version. All regards.

GMagician, 2020-09-19:
Ok, I'll wait for 2.1 then.

Thanks for considering my hint.

To complete it, the TMC register I noticed to change were the ones involved in sensorless homing (I'm almost sure current limit was one of them)

GerogeFu, 2020-09-19:
Ok , i want to know if user power the stepper driver with the power supply , this won't bother them, right ? It only happened when stepper driver power by USB/5v, following 12v/24v.

GMagician, 2020-09-19:
This is how to replicate issue:

USB + 24V (no matter order) and home: everything ok
removed 24V: TMC registers changed.
reapplyed 24V: TMC register still changed
home: sensorless is done with too high current (and I almost sure it's not the only register changed)

GMagician, 2020-09-19:
you may read https://github.com/MarlinFirmware/Marlin/issues/18498 to see how registers change, there is a Marlin log

GMagician, 2020-09-19:
here is a syummary of what is changed after power off
before:
15:05:37.418 : Set current 900 900 900 1000 250
15:05:37.441 : RMS current 887 887 887 994 244
15:05:37.503 : CS actual 14/31 14/31 14/31 8/31 3/31
15:05:37.525 : PWM scale 16 16 16 10 4
15:05:37.556 : vsense 1=.18 1=.18 1=.18 0=.325 1=.18
15:05:37.603 : msteps 16 16 16 16 16
15:05:37.688 : off time 4 4 4 4 4
15:05:37.719 : blank time 24 24 24 24 24
15:05:37.741 : -end 2 2 2 2 2
15:05:37.773 : -start 1 1 1 1 1
15:05:38.058 : Driver registers:
15:05:38.073 : X 0xC0:0E:00:00
15:05:38.073 : Y 0xC0:0E:00:00
15:05:38.089 : Z 0xC0:0E:00:00
15:05:38.089 : Z2 0xC0:08:00:00
15:05:38.089 : E 0xC0:03:00:00
after:
5:06:57.700 : RMS current 1602 1602 1602 994 441
15:06:57.738 : MAX current 2259 2259 2259 1402 622
15:06:57.769 : CS actual 31/31 31/31 31/31 31/31 31/31
15:06:57.784 : PWM scale 36 36 36 36 36
15:06:57.816 : vsense 0=.325 0=.325 0=.325 0=.325 0=.325
15:06:57.869 : msteps 8 8 8 8 8
15:06:57.954 : off time 3 3 3 3 3
15:06:57.985 : blank time 36 36 36 36 36
15:06:58.016 : -end -3 -3 -3 -3 -3
15:06:58.038 : -start 6 6 6 6 6
15:06:58.333 : Driver registers:
15:06:58.339 : X 0xC0:1F:00:00
15:06:58.339 : Y 0xC0:1F:00:00
15:06:58.355 : Z 0xC0:1F:00:00
15:06:58.355 : Z2 0xC0:1F:00:00
15:06:58.370 : E 0xC0:1F:00:00

as you can see are a lot of values

GerogeFu, 2020-09-21:
Thanks for your report. I get it.

GMagician, 2020-11-04:
@GerogeFu sorry to bother, I see that in V2.0 there is no vmot diode protection at all but you can power using usb 5V. I'm expecting that doing such option will kill a lot of tmc drivers. Do you think you will add such diode in new board revisions? Do you think such diode will work on 5V instead 3.3V?

Thanks

Closed 2020-09-19.

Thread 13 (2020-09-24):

Updated info on S6 v2.0 wanted

Bajotaz, 2020-09-24:
I am unable to find any info regarding v2.0.

John-SC077, 2020-09-27:
I also need some help with this release.

I received 3 V2.0 boards yesterday, but cannot move my code to them because the code cannot operate the TMC 5160 drivers on this version.  The same code is operating on V1.2 boards without issue, but the TMC 5160 drivers do not energize the stepper motors when on the V2.0 S6 board.  The remainder of the sketch works perfectly including running the WiFi on the UART port and a connection to another Arduino device on Serial3 (on the EXP1 connector.

GerogeFu, 2020-09-27:
I update the README of S6 , try to follow it.

Bajotaz, 2020-09-27:
> I also need some help with this release.
>
> I received 3 V2.0 boards yesterday, but cannot move my code to them because the code cannot operate the TMC 5160 drivers on this version. The same code is operating on V1.2 boards without issue, but the TMC 5160 drivers do not energize the stepper motors when on the V2.0 S6 board. The remainder of the sketch works perfectly including running the WiFi on the UART port and a connection to another Arduino device on Serial3 (on the EXP1 connector.

//
// Steppers
//
#define X_ENABLE_PIN                        PE9

#if HAS_TMC_UART
  #define X_SERIAL_TX_PIN                   PE8
  #define Y_SERIAL_TX_PIN                   PC4
  #define Y_SERIAL_RX_PIN                   PC4
  #define Z_SERIAL_TX_PIN                   PD12
  #define E0_SERIAL_TX_PIN                  PA15
  #define E1_SERIAL_TX_PIN                  PC5
  #define E2_SERIAL_TX_PIN                  PE0
#endif

Bajotaz, 2020-09-27:
> I update the README of S6 , try to follow it.

Thanks, found my info now.

Closed 2020-10-08.

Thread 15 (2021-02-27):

Ender 5 upgrade

MadeInRu, 2021-02-27:
Dear Fysetc guys,

Can you please assists me. I've ordered your motherboard S6 V2.0 in order to upgrade my Ender 5, and want to know if i connected all the jumpers correctly. Please see the picture.

Also I've ordered TMC 2226 drivers, are they compatible with that motherboard?

Which parts of the software i need to adjust for Ender 5?

With best regards,

Jevgeni
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

GerogeFu, 2021-05-28:
I don't think so , the jumpers for stepper driver are not right.
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
You can check the README here: https://github.com/FYSETC/FYSETC-S6
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

Closed 2021-07-15.

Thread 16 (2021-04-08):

"Cut Jumpers" for 5V AD597K

Jhonno84, 2021-04-08:
Can someone explain in very simple terms how to "cut the jumper" so I can run a PT100 through an AD597K board?

Marconet68, 2021-04-11:
I've put some explanation on "FYSETC" facebook group: [https://www.facebook.com/groups/197476557529090/permalink/812555469354526/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](url).
It will very helpfull that somebody from Fysetc confirm the connection.

But AD597K is for Thermocouple type K not for PT100....
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

Jhonno84, 2021-04-11:
Hi Marco,

Thanks for taking time with me on this..

I seem to have made an incorrect assumption.. When I searched for the AD597 only AD597K came up. So I thought it was the same thing. I have ordered a MAX31865 also..

Jhonno84, 2021-04-30:
I can confirm the above works. I am running an AD597K board, with a PT100, jumper cut and board powered off an alternative 5V supply. Running Klipper, you need to configure the board to 3.3v not 5v as PC0 is 3.3V.

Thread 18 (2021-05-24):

R24 10 K pullup resistors

azwing, 2021-05-24:
The 10K R24 pullup resistors are not populated on board Version 2.0.
This should be reflected in schematics

GerogeFu, 2021-05-28:
See , thanks

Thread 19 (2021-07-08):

New bootloader

GMagician, 2021-07-08:
Hi, not sure this is the right place.
I tryed to upload new bootloader 0x8000 with stcube.
Once loaded, always with dfu and VScode I uploaded Marlin S6_8000 env but once I reboot (boot jumper and power off/on) no usb port happears.

Since it doesn't work I re uploaded boot_10000 and marlin s6 env and it works.

What's wrong?

GMagician, 2021-07-08:
Precompiled Marlin, loaded with stcube, works. Only the source with vscode seems to hang.
I wrote to Marlin github

GerogeFu, 2021-07-09:
Did you try the branch in this repo, and what upstream Marlin are you using? The right one should be bugfix-2.0.x.

GMagician, 2021-07-09:
Marlin in this repo is working, I tryed the very last bugfix in Marlin, compiled for 8000 env, that seems not to work

GerogeFu, 2021-07-12:
Did you raise an issue for Marlin ?

GMagician, 2021-07-12:
I wrote on PR which merged 8000 version, but I think it's good to open an issue

kyon03, 2021-07-13:
same issue whats the solution?

rsdcampos, 2021-07-21:
Same issue for me to. If I use the 0x10000 the eeprom don't save the changes, when I do a M500 it returns "Error writing to EEPROM" and EEPROM datasize error". There are any solution for it?

GerogeFu, 2021-07-22:
Check the PR here https://github.com/MarlinFirmware/Marlin/pull/22421

rsdcampos, 2021-07-22:
>
>
> Check the PR here [MarlinFirmware/Marlin#22421](https://github.com/MarlinFirmware/Marlin/pull/22421)

Nope, I made your changes in Marlin bugfix and used your entire commit using my configurations files without sucess in both, same issue. Just for complete answer, yes, I changed the envs in platformio.ini and tryed both variants without sucess.

GerogeFu, 2021-07-31:
Now should work. Check the [PR](MarlinFirmware/Marlin#22421) there.

GMagician, 2021-07-31:
Yep that solve this

Closed 2021-07-31.

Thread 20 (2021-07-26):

Clipper and new bootloader

asha77, 2021-07-26:
Hi,
i've got error with new bootloader and klipper firmware with S6 board.
Firmware uploaded using STM32cube and DFU.
Sequence:
1. Enter DFU Mode
2. Upload Latest bootloader
3. Restart Board
4. Upload latest klipper compiled firmware. Start address set to 0x08010000
5. Flashing successfull
6. Attach S6 to RPI
7. Starting Klipper, Firmware working OK, I can print
8. When I reboot board with BOOT jumper set to DFU - it goes to DFU mode (expected)
9. Whet I remove DFU Jumper and reboot board - USB cannot detect board anymore. It becomes brick.

I can repeat steps 1-7 to make it work again, but it is not expected scenario.

Please, advice what to do with that, thank you in advance.

GerogeFu, 2021-07-30:
Why you want to set to DFU at step 8?

asha77, 2021-07-30:
Just to check how it starting with and without jumper.
Important note: on step 7 it starts OK from STM32cube, not from hard reset (power cycle reset button).
Steps 8, 9 - made with hard reset.

GerogeFu, 2021-07-31:
You can use our prebuild to test the bootloader: https://github.com/FYSETC/FYSETC-S6/tree/main/firmware/Pre-builds, it is Marlin build, you can send "M105" command to test if board works ok. I double check my side,  it works. And i recommend a hard reset after you flash firmware.

teeedubb, 2022-04-15:
Hi,

I am experiencing the same scenario exactly. Did you ever resolve this?

asha77, 2022-04-15:
Hi, after some manipulations i get board back to work.
Unfortunately i not tried to reproduce this issue, i can't privide any clear instruction to fix it.

teeedubb, 2022-04-15:
Compiling klipper for no bootloader solved the issue for me, it now works after a reboot.

asha77, 2022-07-13:
I got this issue once again. yes, klipper with no bootloader option did it:
- compile klipper.bin with no bootloader
- set BOOT jumper to DFU mode
- ensure DFU mode active: dfu-util -l -v
- flash firmware: dfu-util -d 0483:df11 -a 0 -R -D  klipper_no_bootloader.bin -s0x08000000

After restart S6 octoprint can communicate with klipper.

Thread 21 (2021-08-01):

Missing pinout drawing file

rsdcampos, 2021-08-01:
I like a lot this board, but a thing I miss a lot to use it is a drawing with the correspondent pinout in place, so I wold like to know if you could provide some good stuff in this way.
some like this:
https://github.com/FYSETC/FYSETC-F6/blob/master/images/F6V1.3-PIN.svg
or this:
https://github.com/makerbase-mks/MKS-Robin-E3-E3D/raw/master/hardware/MKS%20Robin%20E3%20V1.0_003/MKS%20Robin%20E3%20V1.0_003%20PIN.pdf
or this:
https://user-images.githubusercontent.com/12979070/68524259-9e103600-02ff-11ea-8348-4f895cb3e100.png

Thanks a lot.

GerogeFu, 2021-08-02:
See, we will add one. You can check the pin at the back of the board first. I will update here if we done.

rsdcampos, 2021-08-02:
Thanks for the fast answer. Not all the pins are available at back of board, for this reason I ask for pinout. For example, I can't know the order of the out pins for the motors, I need to try and if the motor runs inverted I invert the cable, if there are a pin information I could plug without error. This is just a Example, there are many other good reasons to have a good pinout picture or pdf available here.

Thanks.

teeedubb, 2022-03-27:
Hi @GerogeFu,

Any updates to this?

rsdcampos, 2023-02-01:
Hi, I saw the new pinout file and this is the best pinout file I ever seem. Congratulations and thanks to consider my comments.

Closed 2023-02-01.

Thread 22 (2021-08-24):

Info about power supply

luco85, 2021-08-24:
hello I bought a S6 V2.0 board and i have a question about power supply.
Can i use a 24V power supply for power input and a 12V power supply for bed only (using bed in)?
In this configuration the GND must to be common or not? And the hotend’s heater in this configuration (24V in) goes at 24 or 12V?

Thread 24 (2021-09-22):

trouble with bootloader

deniksem, 2021-09-22:
Hi. i trying to flash bootloader and STM32cubeProgrammer sent me an error [https://ibb.co/F38f9KY](url).
Opening and parsing file: Bootloader-FYSETC_S6_10000.hex
  17:21:46 : Error: Parsing fail
  17:21:47 : Error: In line 6434 :
  17:21:47 : Error: parsing count, expecting hex digit, found '_'
what i am doing wrong?

after that my board does not boot anymore but i was reflash it firmware but it doing nothing.
Can anyone save in stm32cubeprogrammer 0-7 INDEX of memories stm(0x08000000, 0x08004000, 0x08008000, 0x0800c000, and other sectors)? Please. help

deniksem, 2021-09-22:
sorry, i dont know why but everytime when i download hex - size was different, only aftep zip downloading i can flash it. Printer is working

Closed 2021-09-22.

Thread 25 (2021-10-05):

Arduino port issue

coolerooney, 2021-10-05:
Hi

added the STMduino library to the Arduino, and can now select the S6 board in the menu
but the arduino IDE does not show any port available

do I still need to flash the firmware?

thx

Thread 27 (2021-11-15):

Connecting a 24V inductive probe to the S6 2.0

cheezebreeze, 2021-11-15:
Yo!

So I'm slightly confused about the documentation regarding this feature:

"Limit switch socket 24V/5V/3.3V optional, ready for more other equipment, such as -inductive sensor, BL-Touch"

I've got a couple LJ12A3-4-Z/BY lying around and the only problem I see in using it, is that the signal going to the MCU would be 24V. I've been looking at the schematic for the board and I can't see there being any components to pull that voltage down.

Am I missing something or is there an undocumented way to connect it without extra components or do I need to solve the 24V to 5V signal some way with extra components?

( The printer is an Ender 3 with the Fysetc S6 2.0 running Klipper. )

maralb1970, 2021-11-15:
When running an inductive sensor on 24V there are a few options (assuming your probe has NPN output):

1) DeLuxe solution: make a small circuitboard with an optocoupler to isolate the 5V circuitry from the 24V supplyvoltage which the Inductive sensor uses

2) Simple solution: Add a schottky diode (BAT46, BAT85, BAT86) in series with the switching line coming from the inductive probe. Connect the banded side from the diode (Kathode) towards the Inductive probe. Please do not connect the diode the other way around as your controllerboard will not like that.

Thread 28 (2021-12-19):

A problem with Marlin 2.0.9.2

NNMale, 2021-12-19:
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
Wrong default TX RX pin definition in latest Marlin version

maralb1970, 2021-12-20:
About this issue, something was going on some time ago:

https://github.com/MarlinFirmware/Marlin/issues/23044

GerogeFu, 2021-12-20:
Oh, thanks for your report, the Marlin version in this repo is really old, i already update the pin define. i will lately push a new verion Marlin to this repo.

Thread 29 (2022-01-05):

SPI3 pins don't work as SPI

rsdcampos, 2022-01-05:
Hi, I have a SPI TFT with touch and SD card, all using SPI for communication. When I use the TFT and touch in SPI1 both works fine, but when I use the SD in the same MISO and MOSI, the TFT and Touch became unstable, so I decided to use the SPI3 (PC10 for SCK, PC11 for MISO and PC12 for MOSI) for SD and SPI 1 for TFT and touch, so I see that the SPI3 didn't work. I tried to invert and use just TFT in SPI3 without sucess.
There are any way to make the SPI3 to work?
I don't use SPI step drives, so, if there are no way to use SPI3, is there are any way to use SPI2?

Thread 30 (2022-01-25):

S6 V2.0 Pinout error

Kosh42, 2022-01-25:
According to this diagram, E2 is PC8:
https://github.com/FYSETC/FYSETC-S6/blob/main/hardware/V2.0/S6%20V2.0%20Postion.pdf

But in this diagram, PC8 is given as the bed heater output: https://github.com/Klipper3d/klipper/blob/master/config/generic-fysetc-s6-v2.cfg

I have found this to be PB15.

Kosh42, 2022-01-25:
Equally, E0 is PB4, not PC7.

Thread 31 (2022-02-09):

I2C data corruption.

Hermiedaddy2, 2022-02-09:
If you use the NVram at location 0x50,  data to all other devices are corrupt.  Meaning I2C is unusable.

To reproduce problem.  Access NVram, then access another device on I2C.  Such as BME280 or DS3231.

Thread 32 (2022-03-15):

I2C with 2.2 library locks up board.

Hermiedaddy2, 2022-03-15:
Try to use more than 2 I2C devices and the board locks up.  this is with the latest 2.2 library .

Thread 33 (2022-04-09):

Firmware not loading

MarkV3082, 2022-04-09:
Hello all I have a Fysetc S6 V2.0 board. The eeprom will not retain the program after reboot. I think I have everything enabled it's just not persistent

Closed 2022-04-11.

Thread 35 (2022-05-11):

S6 Missing klipper bootloader firmware for flashing MCU over Uart

Max-gee, 2022-05-11:
FYSETC S6 is proving a great board for klipper. and in conjunction with a RPI Z2 and Fluid/Mainsail is almost a perfect setup for most people to use or upgrade to.

the only issue thing that stops me recommending this as 100% perfect is that its not currently easy to upgrade the MCU firmware when klipper is updated without disconnecting the board from UART and rejumpering to setup for USB.

Section 3.3.2 of FYSETC's own wiki states this should be possible
_The UART socket next to the limit switch can be used to connect serial devices such as the wifi module, or **to update the firmware through the serial port.**_

Recently FYSETC released a bootloader compiled for the similar Spider board which uses the same MCU as the S6.

therefore quick questions :-
1. Can anyone tell me if a suitable equivalent is available for the S6 that i'm missing or havnt found
2. could I load the Spiders bootloader firmware  (klipper-32k-Uart.bin) on the S6
3. How involved would it be to compile a suitable bootloader for the S6 that enables serial uart flashing
and finally is there any other way to flash over the RPI serial UART that would work without needing a special bootloader ?

teeedubb, 2022-05-14:
I too am interested in this. Disappointed that the wiki states that it is possible, but I have not found a way to do so.

Max-gee, 2022-10-26:
No solution but it's not on fysetc, after researching it's clear that
almost all MCU's cant be flashed over uart as they needs a special " data
stream" sent over USB to signal the MCU to prepare to go into flashing mode.

Over USB that's doable but not serial over uart

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

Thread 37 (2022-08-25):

Flash marlin hangs bootloader

GMagician, 2022-08-25:
I'm facing a very weird issue with bootloader. I'm using an old 60x sd card, 256MB, FAT32, with firmware.bin file in it.
When I turn off and on it seems to hang (SD is on LCD).
During boot lcd is clean and stay clean
Very often it hangs, some time boot without updating firmware (rare) and some time it works correctly.

Anyone else had this issue?

Is boot source available that may let me fix it by myself?

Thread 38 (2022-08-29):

FYSETC S6 2.0 and TMC2209V3.1 - TMC CONNECTION ERROR

Leidge, 2022-08-29:
I have the FYSETC S6 2.0 card and I'm trying to use the TMC2209 V3.1 driver
I'm using the FYSETC MINI 12864 V2.1 panel with SDCARD.
The TMC CONNECTION ERROR message appears on the panel when I turn on the card.

I'm trying to test the engines with Marlin BUGFIX 2.0 and 2.1.
It is returning the same error.

I always get the message 'TMC CONNECTION ERROR'.
Even if I put it in the 24v source with the pins in DC5V or in the USB.
Even if I put the pin on 5V and DC5V.

I'm trying to run TMC2209 V3.1 in UART.
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

igor-arkhipov, 2023-01-17:
Any solution?

Closed 2022-09-22.

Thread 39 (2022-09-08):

Error message while trying to flash the FYSETEC S6 V2.1 with STM32CuveProgrammer

pilleway, 2022-09-08:
Hi to all.
Help will be advance appreciated.
My project is a OnStep conversion for my telescope to replace DC motors with Step motors.
Trying to flash my board I get the following meesage,
 14:39:33 : RTS low
  14:39:33 : DTR low
  14:39:33 : Serial Port COM6 is successfully opened.
  14:39:33 : Port configuration: parity = none, baudrate = 9600, data-bit = 8,                     stop-bit = 1.0, flow-control = off
  14:39:35 : Timeout error occured while waiting for acknowledgement.
  14:39:35 : Timeout error occured while waiting for acknowledgement.
  14:39:35 : Error: Activating device: KO. Please, verify the boot mode configuration and check the serial port configuration. Reset your device then try again...
As it says port is oppen, but do not know what to do! I looked to assure the jumper in BOOT0 was porperly done, also have 5v thrugh USB, verified cable connection, Also I had reinstalled SMT32CubeProgrammer, all my thoughts to define the problem had exausted.
As you can see, I'm very limited and would like to flash the board and get to next step, to be able to do bench test.
All recomendations and help will be appreciated.
Miguel.

pilleway, 2022-09-09:
The instruccions I have followe are OnStep instrucctions "For the STM32F446 FYSETC S6:" on https://onstep.groups.io/g/main/wiki/3915

Regards

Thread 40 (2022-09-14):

Fysetc S6 and BL Touch

Leidge, 2022-09-14:
I'm having a problem.
I installed the cables as shown in the figure below:
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

BL Touch is working.
I can test it out.
But when the BL TOUCH touches the table, the Z Axis keeps descending without stopping.
I have to turn off the printer quickly.

Estou usando o TMC 2209 V3.1.

Closed 2022-09-22.

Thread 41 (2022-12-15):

Platformio INI settings help - program runs when flashed from Arduino but not PlatformIO

MATT-ER-HORN, 2022-12-15:
After a bit work I was able to get a generic "blink.ino" sketch uploaded and running when using the Arudino IDE and the settings found here: [](https://onstep.groups.io/g/main/message/43912) and changing the upload address to 0x08010000 in the "stm32CubeProg.sh" script. ( 0x08008000 doesn't work even when I use the newer bootloader, not sure why)

However when I upload the same code using platformio the program doesn't run after uploading. Here is my current is .ini file for platformio:

[env:fysetc_s6]
platform = ststm32
board = fysetc_s6
framework = arduino
upload_protocol = dfu
board_upload.offset_address = 0x8010000
build_flags = -D PIO_FRAMEWORK_ARDUINO_ENABLE_CDC -Os

Does anyone have any tips to get the DFU upload working in plaformio for the S6? I assume I could use the same .ini which is used for the marlin build but I can't seem to figure out all the settings since many of the settings are found in separate scripts called by the ini file.

**The output from the terminal during the upload:**

CONFIGURATION: https://docs.platformio.org/page/boards/ststm32/fysetc_s6.html
HARDWARE: STM32F446VET6 168MHz, 128KB RAM, 512KB Flash
DEBUG: Current (blackmagic) External (blackmagic, cmsis-dap, jlink, stlink)
PACKAGES:
 - framework-arduinoststm32 @ 4.20200.221104 (2.2.0)
 - framework-cmsis @ 2.50700.210515 (5.7.0)
 - tool-dfuutil @ 1.11.0
 - tool-openocd @ 2.1100.211028 (11.0)
 - tool-stm32duino @ 1.0.2
 - toolchain-gccarmnoneeabi @ 1.90201.191206 (9.2.1)
LDF: Library Dependency Finder -> https://bit.ly/configure-pio-ldf
LDF Modes: Finder ~ chain, Compatibility ~ soft
Found 11 compatible libraries
Scanning dependencies...
No dependencies
Building in release mode
MethodWrapper(["checkprogsize"], [".pio\build\fysetc_s6\firmware.elf"])
Advanced Memory Usage is available via "PlatformIO Home > Project Inspect"
RAM:   [          ]   3.2% (used 4184 bytes from 131072 bytes)
Flash: [          ]   5.0% (used 26164 bytes from 524288 bytes)
.pio\build\fysetc_s6\firmware.elf  :

section              size        addr

.isr_vector           452   134217728

.text               23744   134218180

.rodata              1880   134241924

.ARM.extab              0   134243804

.ARM                    8   134243804

.preinit_array          0   134243812

.init_array            20   134243812

.fini_array             8   134243832

.data                 540   536870912

.bss                 3644   536871452

.noinit                 0   536875096

._user_heap_stack    1536   536875096

.ARM.attributes        48           0

.comment              102           0

.debug_frame         1360           0

Total               33342
<lambda>(["upload"], [".pio\build\fysetc_s6\firmware.bin"])
AVAILABLE: blackmagic, cmsis-dap, dfu, jlink, serial, stlink
CURRENT: upload_protocol = dfu
"C:\Users\User\.platformio\packages\tool-dfuutil\bin\dfu-util" -d 0x0483:0xDF11 -a 0 -s 0x8010000:leave -D "D:\onedrive\OneDrive - UBC\Documents\PlatformIO\Projects\s6_test_3\.pio\build\fysetc_s6\firmware.bin"
dfu-util 0.11

Copyright 2005-2009 Weston Schmidt, Harald Welte and OpenMoko Inc.
Copyright 2010-2021 Tormod Volden and Stefan Schmidt
This program is Free Software and has ABSOLUTELY NO WARRANTY
Please report bugs to http://sourceforge.net/p/dfu-util/tickets/

Opening DFU capable USB device...
Device ID 0483:df11
Device DFU version 011a
Claiming USB DFU Interface...
Setting Alternate Interface #0 ...
Determining device status...
DFU state(10) = dfuERROR, status(10) = Device's firmware is corrupt. It cannot return to run-time (non-DFU) operations
Clearing status
Determining device status...
DFU state(2) = dfuIDLE, status(0) = No error condition is present
DFU mode device DFU version 011a
Device returned transfer size 2048
DfuSe interface name: "Internal Flash  "
Downloading element to address = 0x08010000, size = 26652

Erase           [                         ]   0%            0 bytes
Erase           [                         ]   0%            0 bytes
Erase           [=                        ]   7%         2048 bytes
Erase           [===                      ]  15%         4096 bytes
Erase           [=====                    ]  23%         6144 bytes
Erase           [=======                  ]  30%         8192 bytes
Erase           [=========                ]  38%        10240 bytes
Erase           [===========              ]  46%        12288 bytes
Erase           [=============            ]  53%        14336 bytes
Erase           [===============          ]  61%        16384 bytes
Erase           [=================        ]  69%        18432 bytes
Erase           [===================      ]  76%        20480 bytes
Erase           [=====================    ]  84%        22528 bytes
Erase           [=======================  ]  92%        24576 bytes
Erase           [======================== ]  99%        26624 bytes
Erase           [=========================] 100%        26652 bytes
Erase    done.

Download        [                         ]   0%            0 bytes
Download        [=                        ]   7%         2048 bytes
Download        [===                      ]  15%         4096 bytes
Download        [=====                    ]  23%         6144 bytes
Download        [=======                  ]  30%         8192 bytes
Download        [=========                ]  38%        10240 bytes
Download        [===========              ]  46%        12288 bytes
Download        [=============            ]  53%        14336 bytes
Download        [===============          ]  61%        16384 bytes
Download        [=================        ]  69%        18432 bytes
Download        [===================      ]  76%        20480 bytes
Download        [=====================    ]  84%        22528 bytes
Download        [=======================  ]  92%        24576 bytes
Download        [======================== ]  99%        26624 bytes
Download        [=========================] 100%        26652 bytes
Download done.
File downloaded successfully
Submitting leave request...
Transitioning to dfuMANIFEST state
====================================================================================== [SUCCESS] Took 12.91 seconds ======================================================================================
 *  Terminal will be reused by tasks, press any key to close it.

**And the blink script I am trying to upload that works using the Arduino IDE**
#include <Arduino.h>
/*
  Blink
  This example code is in the public domain.

  https://www.arduino.cc/en/Tutorial/BuiltInExamples/Blink
*/

// the setup function runs once when you press reset or power the board
void setup() {
  // initialize digital pin LED_BUILTIN as an output.
  pinMode(PB3, OUTPUT);
}

// the loop function runs over and over again forever
void loop() {
  digitalWrite(PB3, HIGH);  // turn the LED on (HIGH is the voltage level)
  delay(1000);                      // wait for a second
  digitalWrite(PB3, LOW);   // turn the LED off by making the voltage LOW
  delay(1000);                      // wait for a second
}
Thanks for your help!

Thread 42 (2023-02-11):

FAN0, FAN1, HotBed, HotEnd pins issue

xsfunc, 2023-02-11:
Klipper
Fysetc S6 v2.1

FAN0, FAN1, HotBed, HotEnd pins doesn't work. Stepper, endstop, termistor, fan2 works well.

```
[heater_bed]
heater_pin: PC8
sensor_type: EPCOS 100K B57560G104F
sensor_pin: PC3
control: watermark
min_temp: 0
max_temp: 100

[extruder]
step_pin: PD5
dir_pin: !PD6
enable_pin: !PD4
microsteps: 16
rotation_distance: 33.500
nozzle_diameter: 0.400
filament_diameter: 1.750

heater_pin: PB15
sensor_type: EPCOS 100K B57560G104F
sensor_pin: PC0
control: pid
# tuned for stock hardware with 200 degree Celsius target
pid_Kp: 21.527
pid_Ki: 1.063
pid_Kd: 108.982
min_temp: 0
max_temp: 250
```

A problem in the software or a marriage of the board?

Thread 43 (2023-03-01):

Klipper gives "Unable to write tmc spi 'stepper_x' register GLOBALSCALER" error for TMC 5160 driver

alphanci, 2023-03-01:
I am using Klipper firmware for Fysetc S6(version 2.1) board. I installed Fysetc S5160(version 1.2) driver to X and Y driver sockets. I am getting "Unable to write tmc spi 'stepper_x' register GLOBALSCALER" error in both slots. 4 jumpers are installed on bottom positions as described in the README. TMC 2209 drivers work in these sockets with UART configuration. I tried 4 different 5160 drivers so this shouldn't be a faulty driver issue.

Klipper docs say that this error might be the result of shared SPI bus:

> Note that if the driver is on a shared SPI bus with multiple devices then be sure to fully configure every device on that shared SPI bus in Klipper. If a device on a shared SPI bus is not configured, then it may incorrectly respond to commands not intended for it and corrupt the communication to the intended device. If there is a device on a shared SPI bus that can not be configured in Klipper, then use a [static_digital_output config section](https://www.klipper3d.org/Config_Reference.html#static_digital_output) to set the CS pin of the unused device high (so that it will not attempt to use the SPI bus). The board's schematic is often a useful reference for finding which devices are on an SPI bus and their associated pins.

I looked at the schematic but I couldn't find out if the SPI bus is shared. Sample config [file](https://github.com/Klipper3d/klipper/blob/master/config/generic-fysetc-f6.cfg) for F6 has a static_digital_output section but sample config [file](https://github.com/Klipper3d/klipper/blob/master/config/generic-fysetc-s6.cfg) for S6 doesn't have it so I am not sure.

My printer config file:

```
[mcu]
serial: /dev/serial/by-id/usb-Klipper_stm32f446xx_32005B000F51303530323539-if00
restart_method: command

#[mcu]
#serial: /dev/ttyAMA0
#restart_method: command

[force_move]
enable_force_move: True

[printer]
kinematics: corexy
max_velocity: 300
max_accel: 3000
max_z_velocity: 25
max_z_accel: 30

[stepper_x]
step_pin: PE11
dir_pin: PE10
enable_pin: !PE9
microsteps: 16
rotation_distance: 40
endstop_pin: ^PA2
position_endstop: 0
position_max: 200
#homing_speed: 50

[tmc5160 stepper_x]
spi_bus: spi1
cs_pin: PE7
run_current: 0.8

[stepper_y]
step_pin: PD8
dir_pin: PB12
enable_pin: !PD9
microsteps: 16
rotation_distance: 40
endstop_pin: ^PA3
position_endstop: 0
position_max: 200
homing_speed: 50

[tmc5160 stepper_y]
spi_bus: spi1
cs_pin: PE15
run_current: 0.8

[stepper_z]
step_pin: PD14
dir_pin: PD13
enable_pin: !PD15
microsteps: 16
rotation_distance: 8
endstop_pin: ^PA0
position_endstop: 0.5
position_max: 200

[tmc2209 stepper_z]
uart_pin: PD12
run_current: 0.8
interpolate: False

[manual_stepper ex0]
step_pin: PD5
dir_pin: PD6
enable_pin: !PD4
rotation_distance: 5
microsteps: 8

[tmc2209 manual_stepper ex0]
uart_pin: PA15
run_current: 0.8
interpolate: False

[manual_stepper ex1]
step_pin: PE6
dir_pin: PC13
enable_pin: !PE5
rotation_distance: 5
microsteps: 8

[tmc2209 manual_stepper ex1]
uart_pin: PC5
run_current: 0.8
interpolate: False

[manual_stepper tool_lock_stepper]
step_pin: PE2
dir_pin: PE4
enable_pin: !PE3
endstop_pin: ^PA1
rotation_distance: 5
microsteps: 8

[tmc2209 manual_stepper tool_lock_stepper]
uart_pin: PE0
run_current: 0.8
interpolate: False

#[tmc2209 stepper_z]
#uart_pin: PD10
#run_current: 0.8
#interpolate: False

#[extruder]
#step_pin: PE2
#dir_pin: PE4
#enable_pin: !PE3
#microsteps: 16
#rotation_distance: 33.500
#nozzle_diameter: 0.400
#filament_diameter: 1.750
#heater_pin: PB15
#sensor_type: PT1000
#sensor_pin: PC0
#pullup_resistor: 4700
#control: pid
#pid_Kp: 22.2
#pid_Ki: 1.08
#pid_Kd: 114
#min_temp: 0
#max_temp: 500

#[heater_bed]
#heater_pin: PC8
#sensor_type: EPCOS 100K B57560G104F
#sensor_pin: PC3
#control: watermark
#min_temp: 0
#max_temp: 130

#[fan]
#pin: PB0
#hardware_pwm: True
#cycle_time: 0.00004

#[force_move]
#enable_force_move: True

[virtual_sdcard]
path: ~/gcode_files

[display_status]
[pause_resume]

[gcode_macro CANCEL_PRINT]
description: Cancel the actual running print
rename_existing: CANCEL_PRINT_BASE
gcode:
  TURN_OFF_HEATERS
  CANCEL_PRINT_BASE

```

My log file:
[klippy.log](https://github.com/FYSETC/FYSETC-S6/files/10860042/klippy.log)

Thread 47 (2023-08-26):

S6 v2.1 - cant get in DFU Mode

MightyMirko, 2023-08-26:
Hello,

ive been following

>
```
Enter DFU mode first

    First power off the board
    Set jumper on 5v pin and DC5V
    Place jumper on BT0 to 3.3V pin
    Connect USB cable to the board and your computer
    Power up the board with 24v
```

I tried 2 different cables but i cant get it in dfu mode. is there anything different on 2.1?

MightyMirko, 2023-08-27:
https://github.com/FYSETC/FYSETC-SPIDER/issues/22#issuecomment-877506960

this is the solution

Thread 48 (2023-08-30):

Onstep ST4 connection

Luporosso76, 2023-08-30:
HI,
I read on the onStep wiki that it is possible to connect the ST4 to the board.
The connection requires the use of "2.2K Ohm bussed resistor network 5-pin".
I wanted to know:

1 - Is it necessary even if SHC is not used?
2 - How do you connect the cables of the ST4 cable with the bussed resistor and then everything on the exp1?

Thanks in advance
Alessandro

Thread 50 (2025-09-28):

Fystec S6 V2.0 Pinout?

lolwutboi987, 2025-09-28:
Hi,
I'm in the process of configuring SPI via klipper with my fystec v2.0, which i have hooked up to my BTT TMC 5160T Plus. I tried using the 2.1 pinout, however I'm getting returned Unable to write tmc spi 'stepper_x' register GCONF, which tells me the board cannot communicate with the TMC 5160 plus. For stepper X im using the CS pin PE7, and spi_bus spi1. I've also tried defining software SPI as follows:
#spi_software_mosi_pin: PE14
#spi_software_miso_pin: PE13
#spi_software_sclk_pin: PE12
and no matter where I search, I cannot find the pinout diagram for the s6 v2.0.

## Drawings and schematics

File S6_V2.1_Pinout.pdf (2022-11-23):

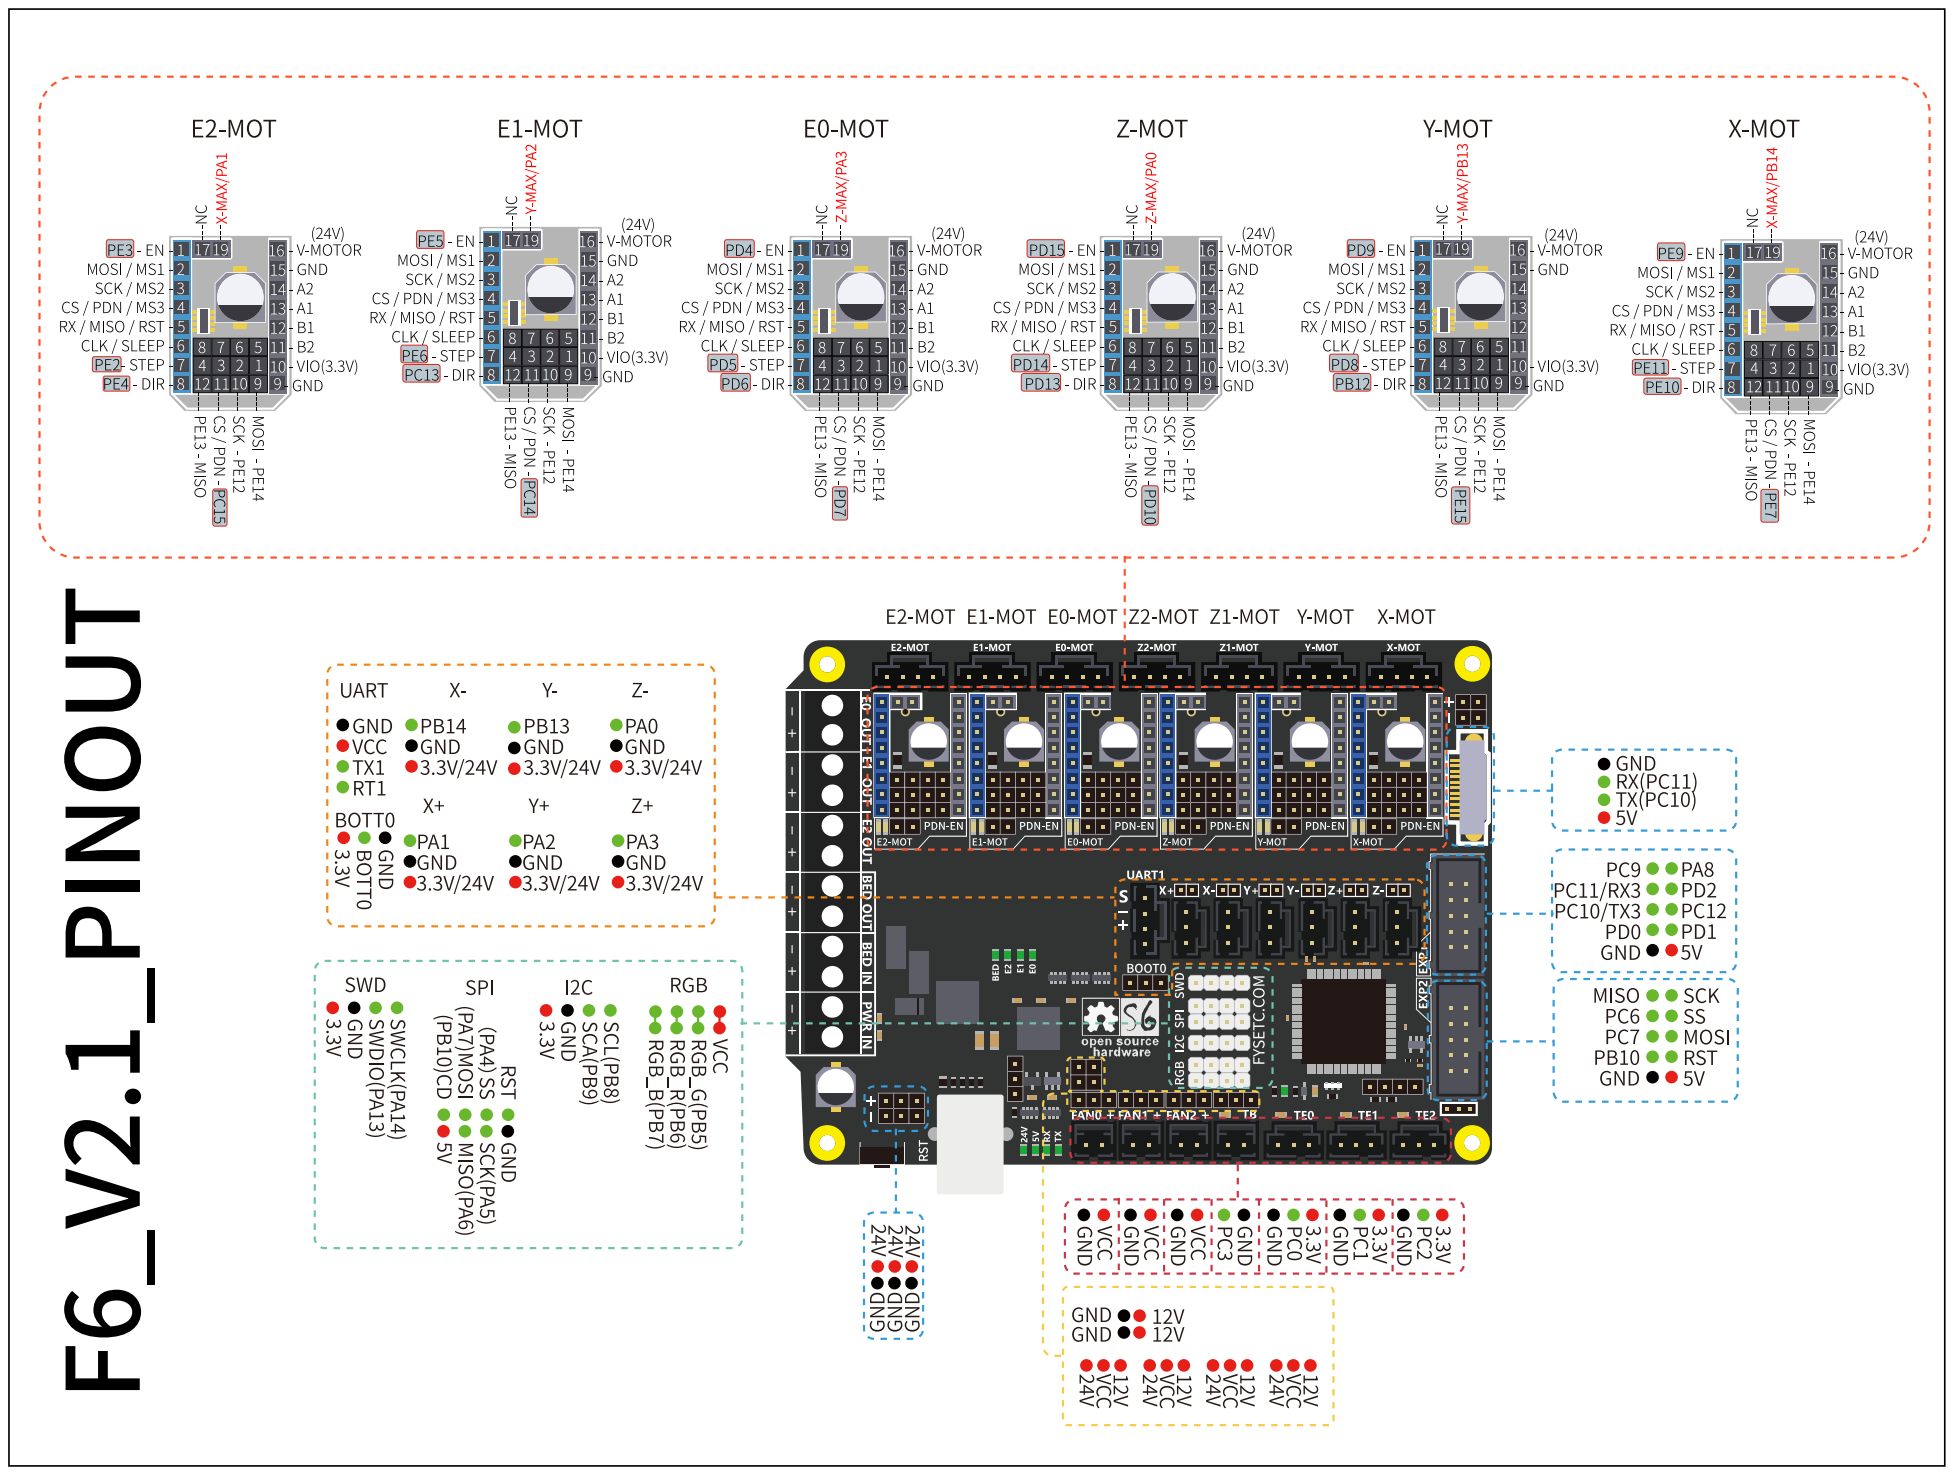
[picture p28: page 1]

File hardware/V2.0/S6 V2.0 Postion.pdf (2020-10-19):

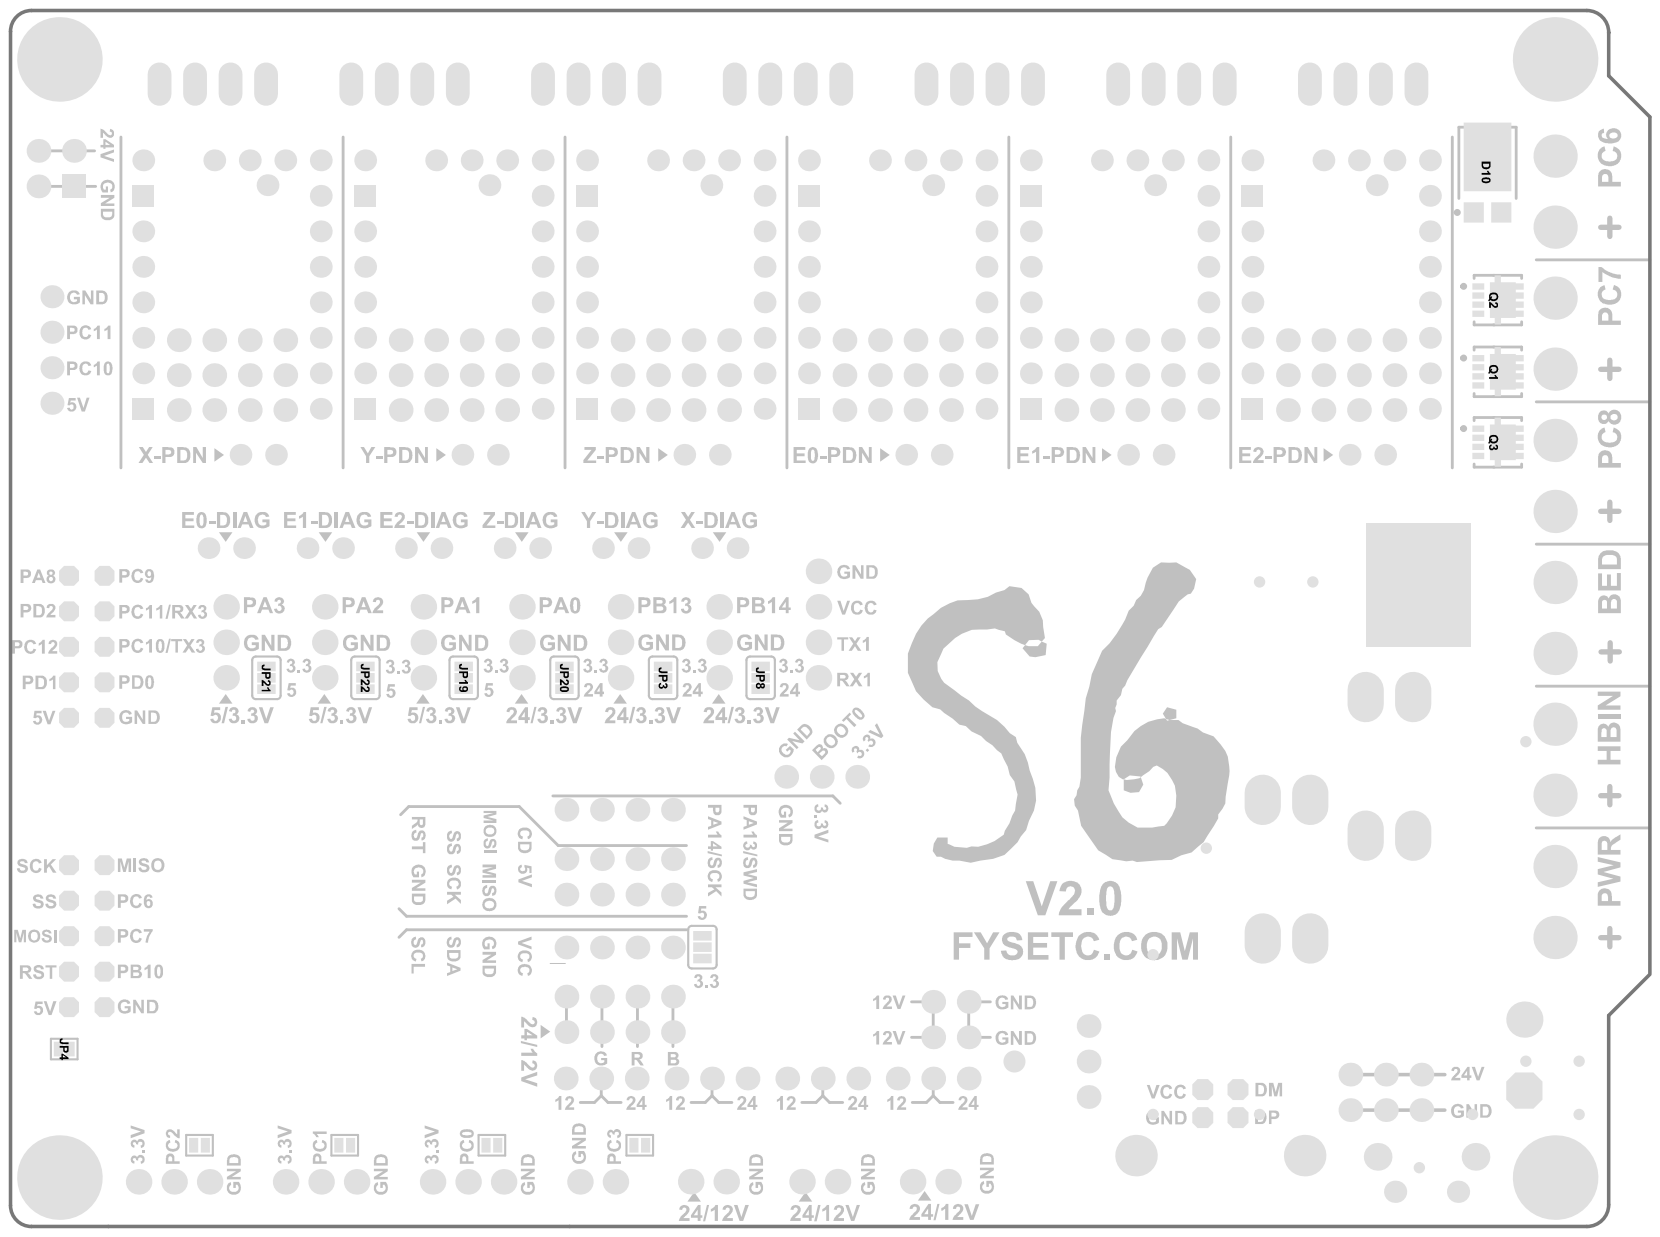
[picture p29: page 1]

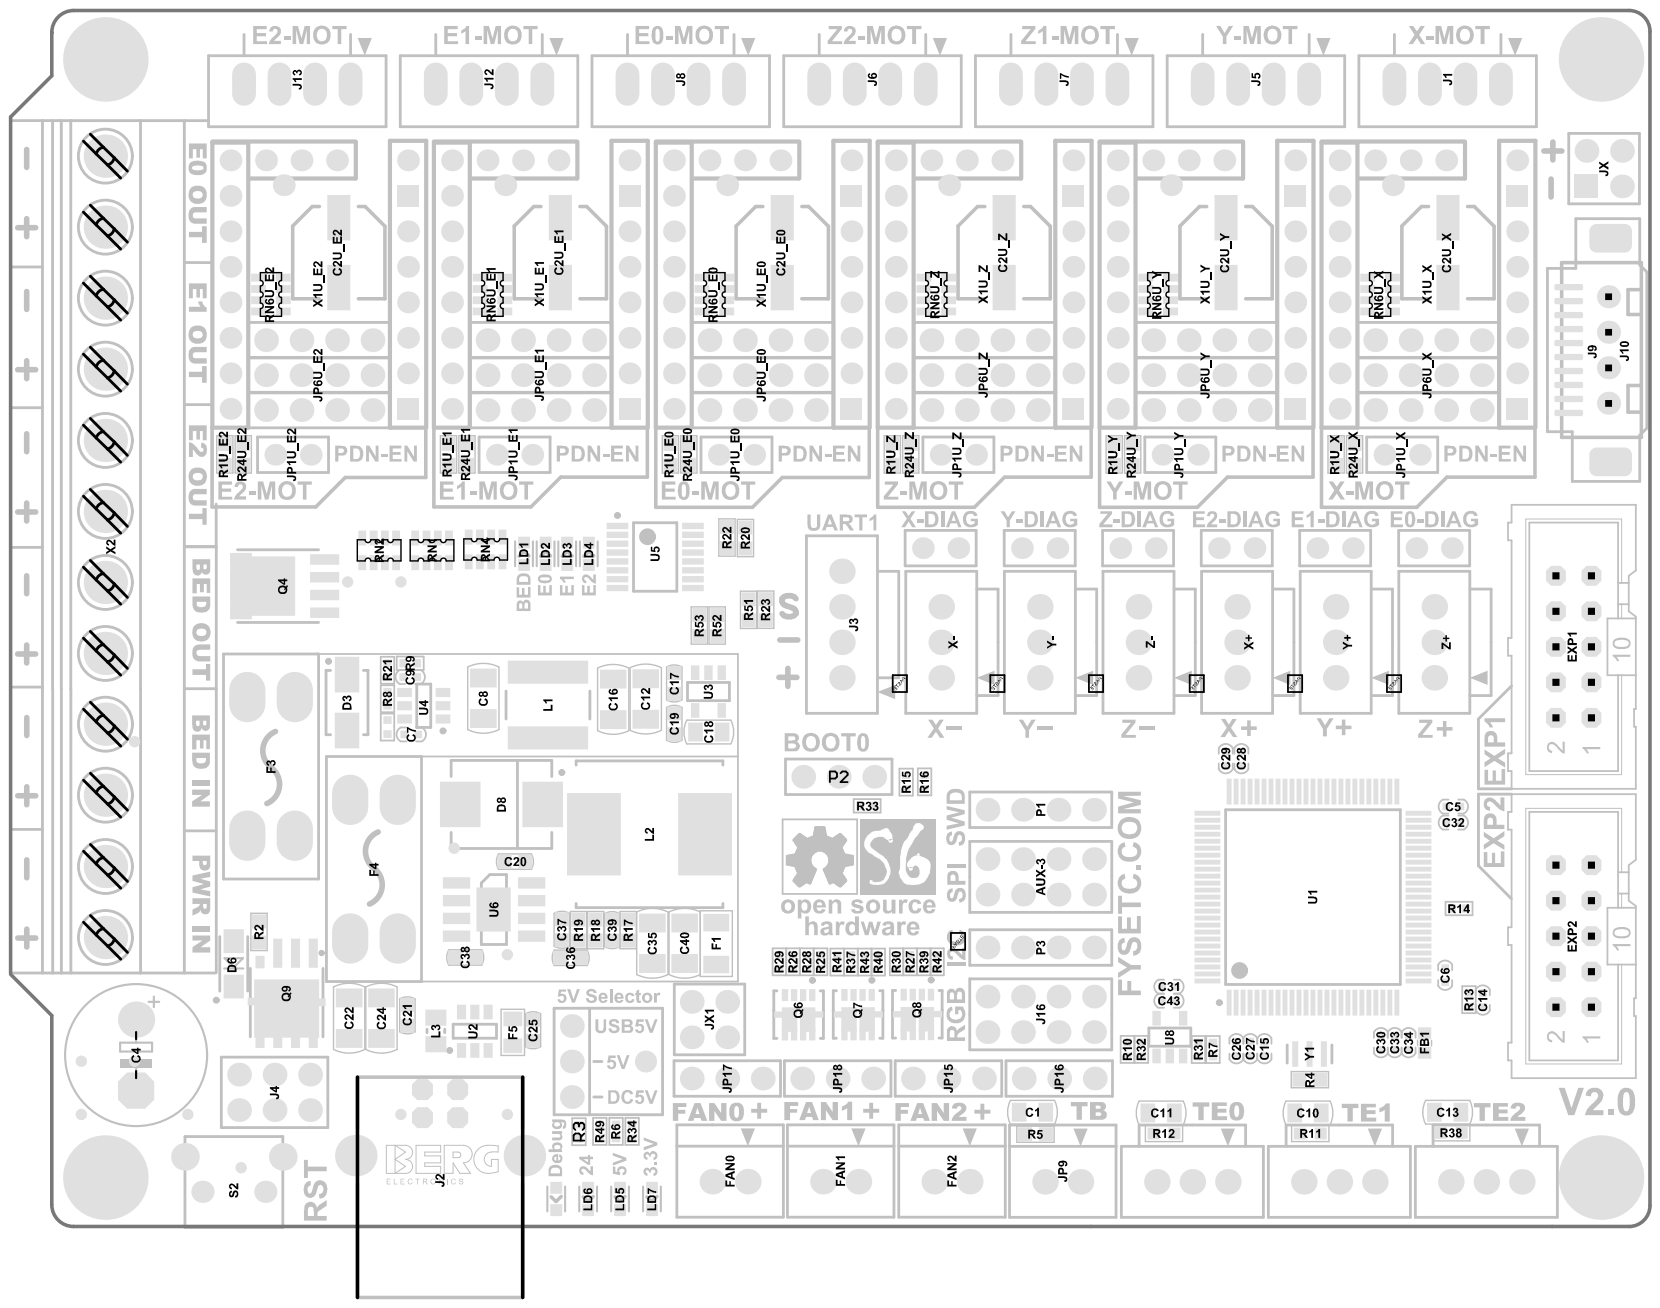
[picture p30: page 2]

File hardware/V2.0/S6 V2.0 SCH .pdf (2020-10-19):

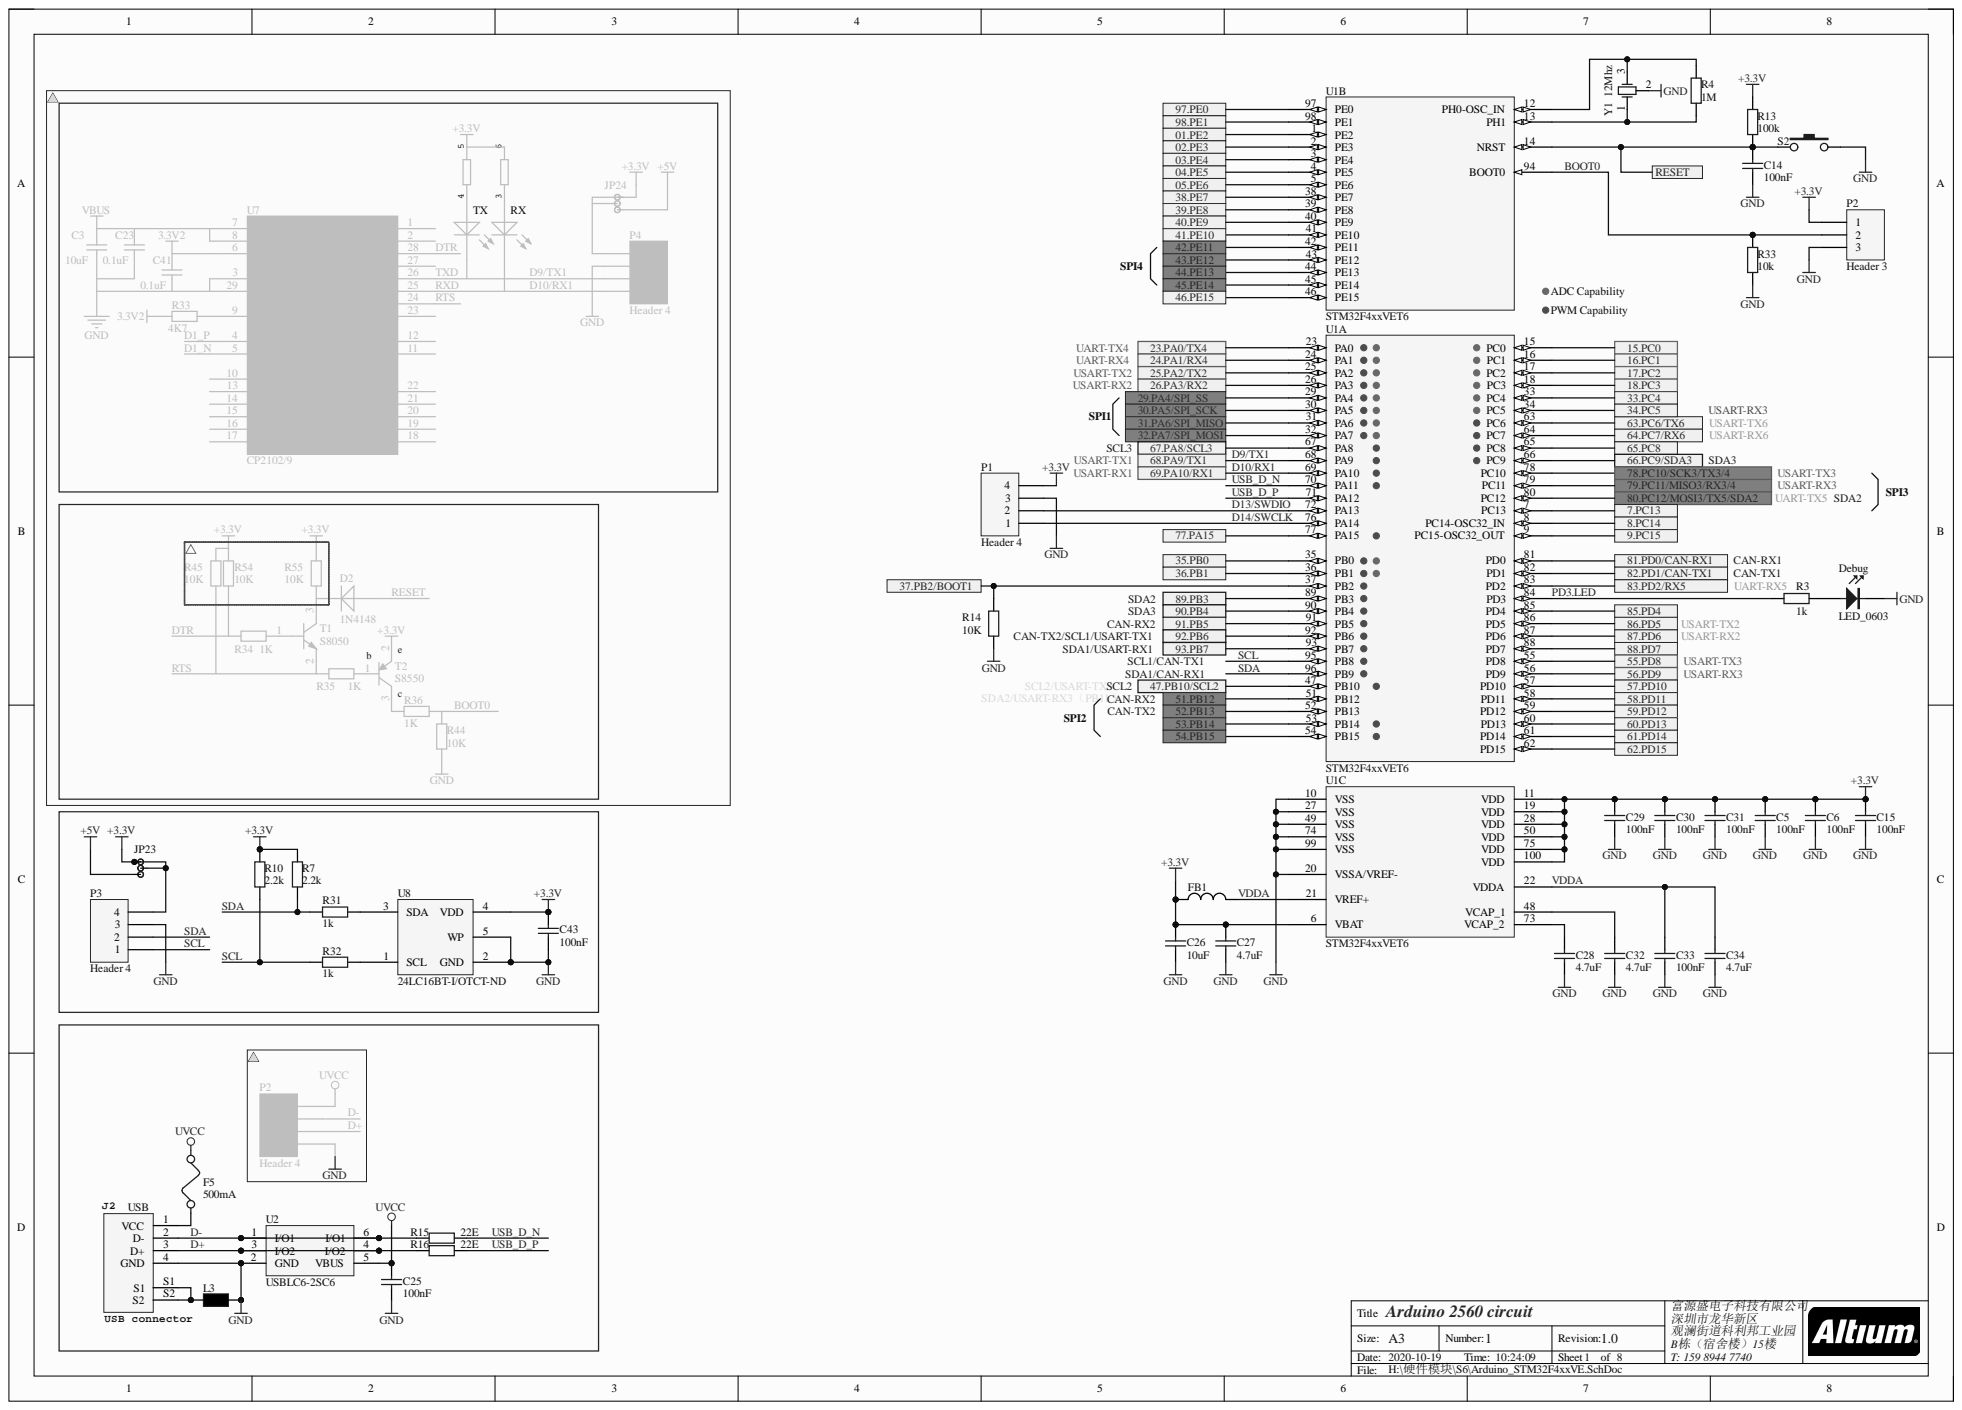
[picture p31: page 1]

01.PE2 | PE2 1
02.PE3 | PE4 3 | BOOT0

05.PE6 | PE7 38
38.PE7 | PE8 39

32.PA7/SPI_MOSI | | 64.PC7/RX6
67.PA8/SCL3 | PA8 67 | 65.PC8

35.PB0 | | PB1 36 | | 81.PD0/CAN-RX1
36.PB1 | | | | 82.PD1/CAN-TX1

89.PB3 | PB4 90
91.PB5 | | PB5 91 | | 86.PD5
92.PB6 | | PB6 92 | | 87.PD6
93.PB7 | SCL | PB8 95 | | 88.PD7

47.PB10/SCL2 | PB12 51 | 57.PD10
51.PB12 | PB13 52 | 58.PD11
52.PB13 | | 59.PD12
53.PB14 | PB14 53 | 60.PD13
54.PB15 | | 61.PD14

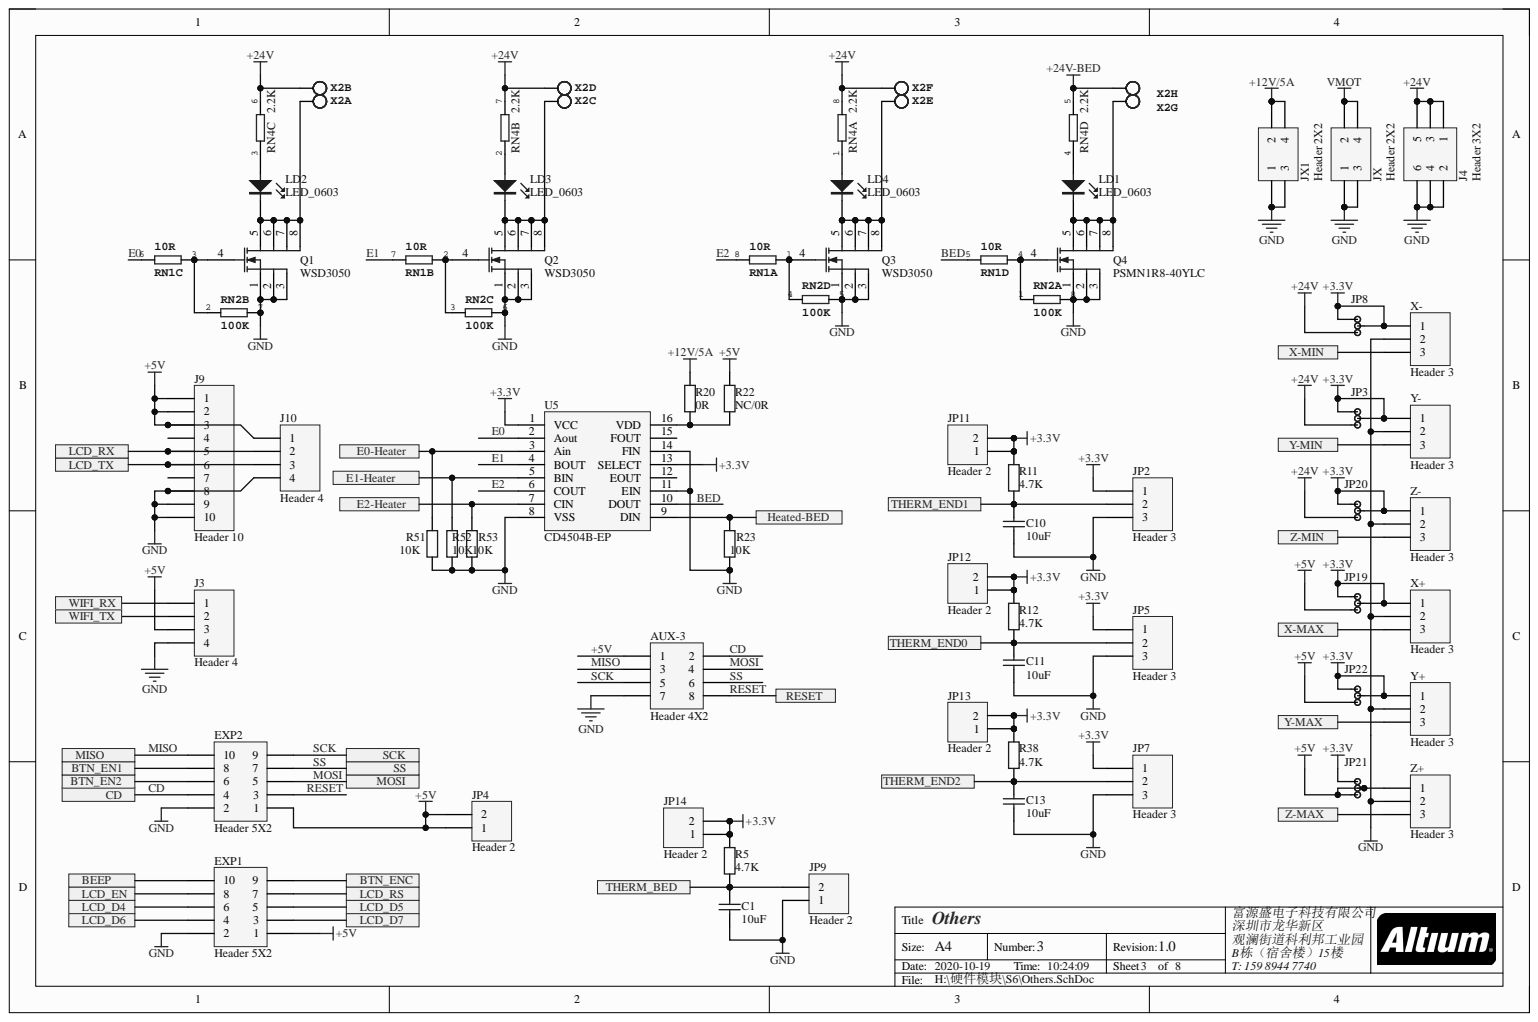
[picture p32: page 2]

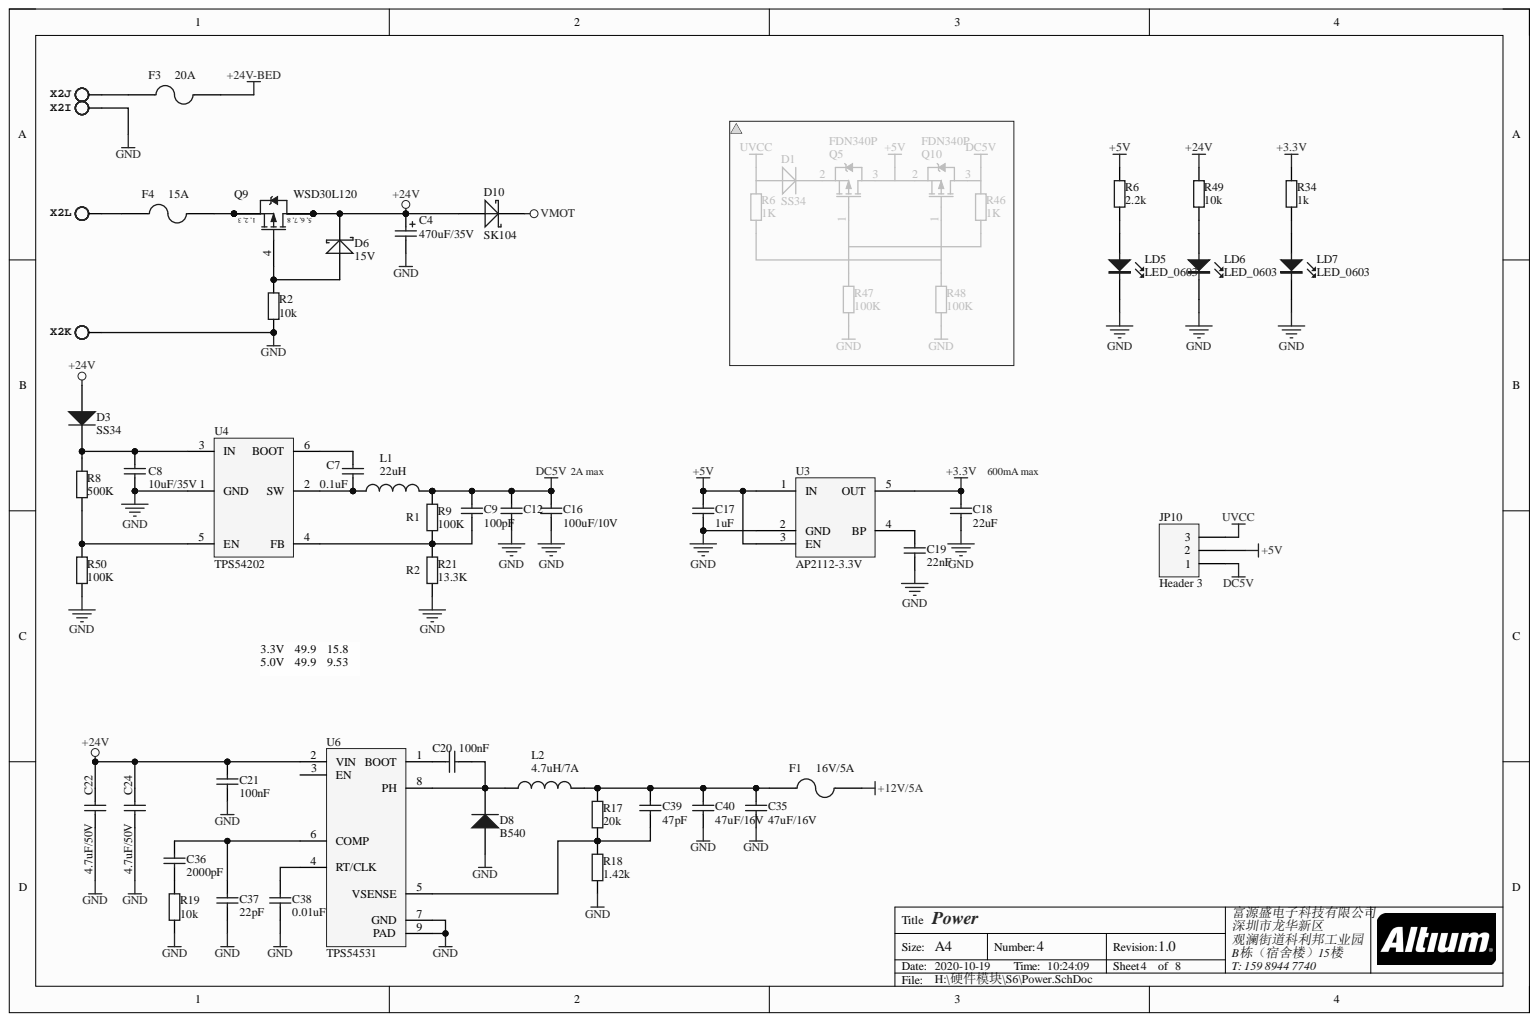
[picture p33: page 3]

RT/CLK 4

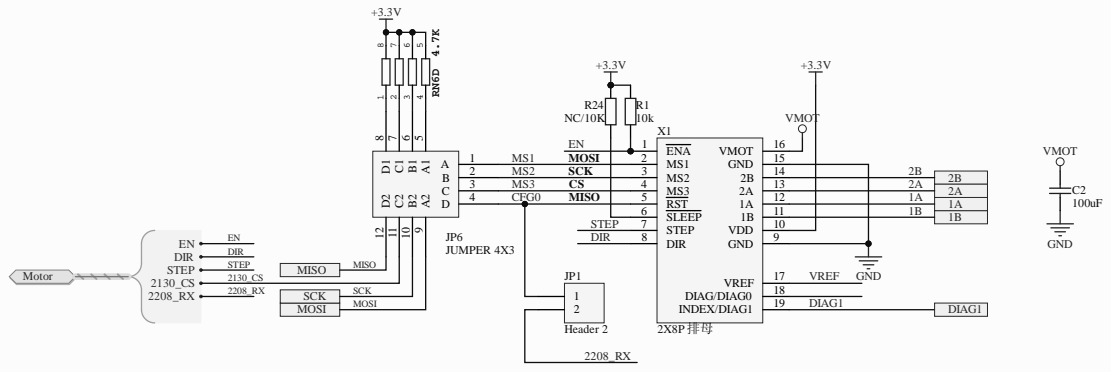
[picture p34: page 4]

2 MS2 SC K | 3 | 1 4
3 MS3 C S | 4 | 1 3 | | 2 A
4 CFG 0 ISO M | 5 | 1 2 | | 1 A

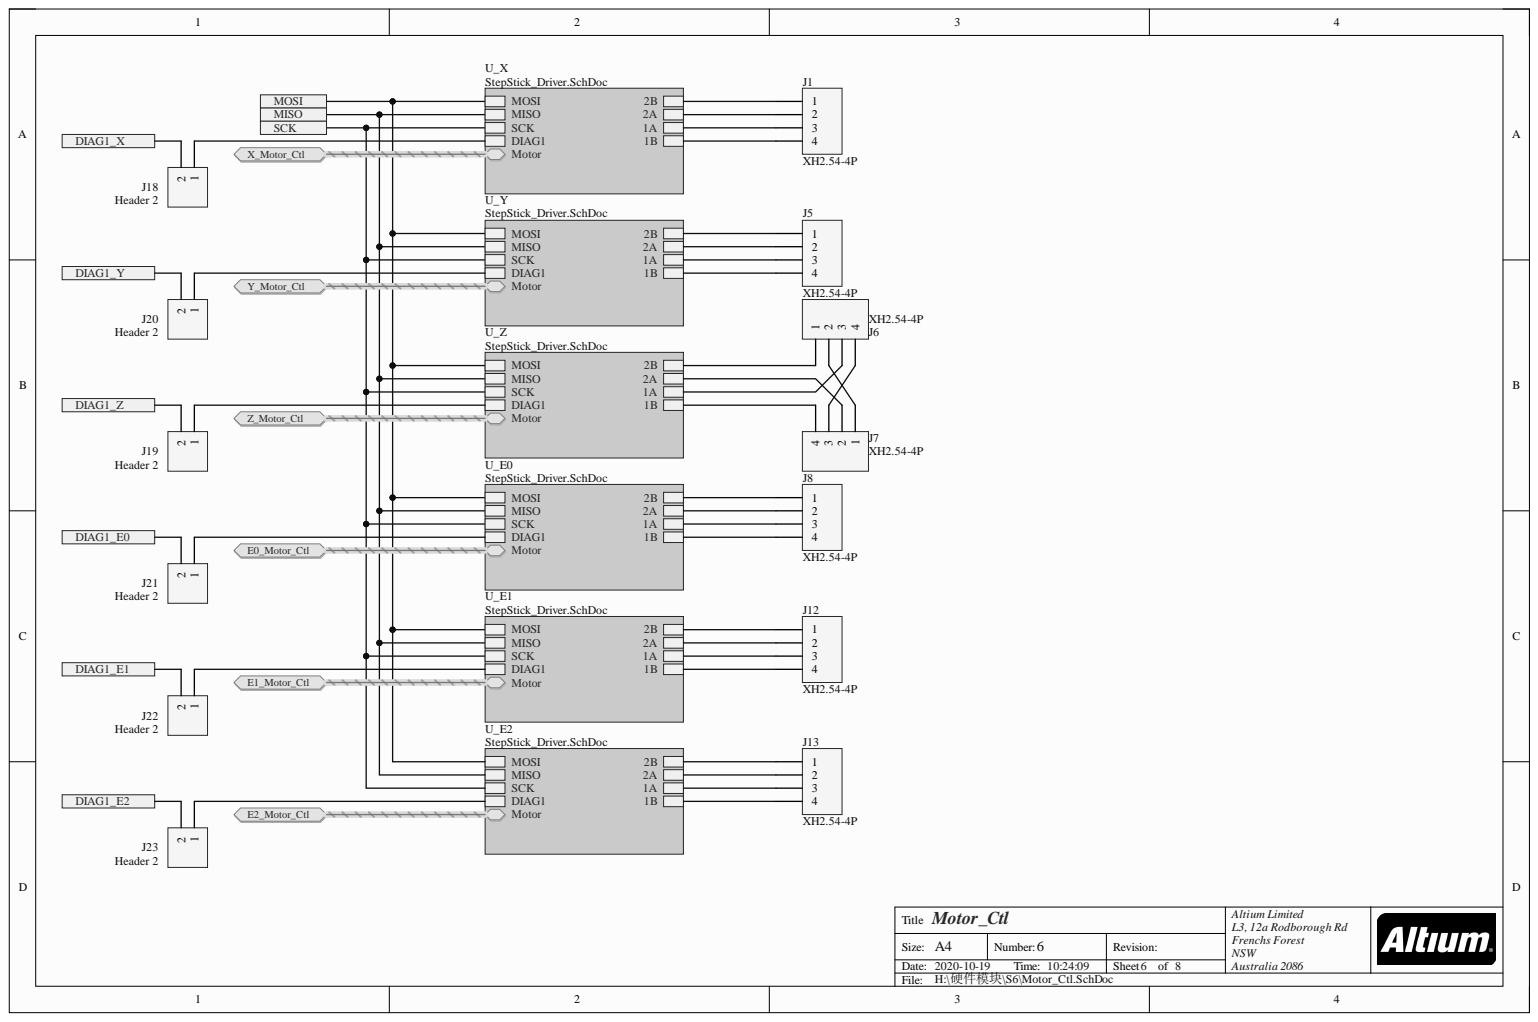
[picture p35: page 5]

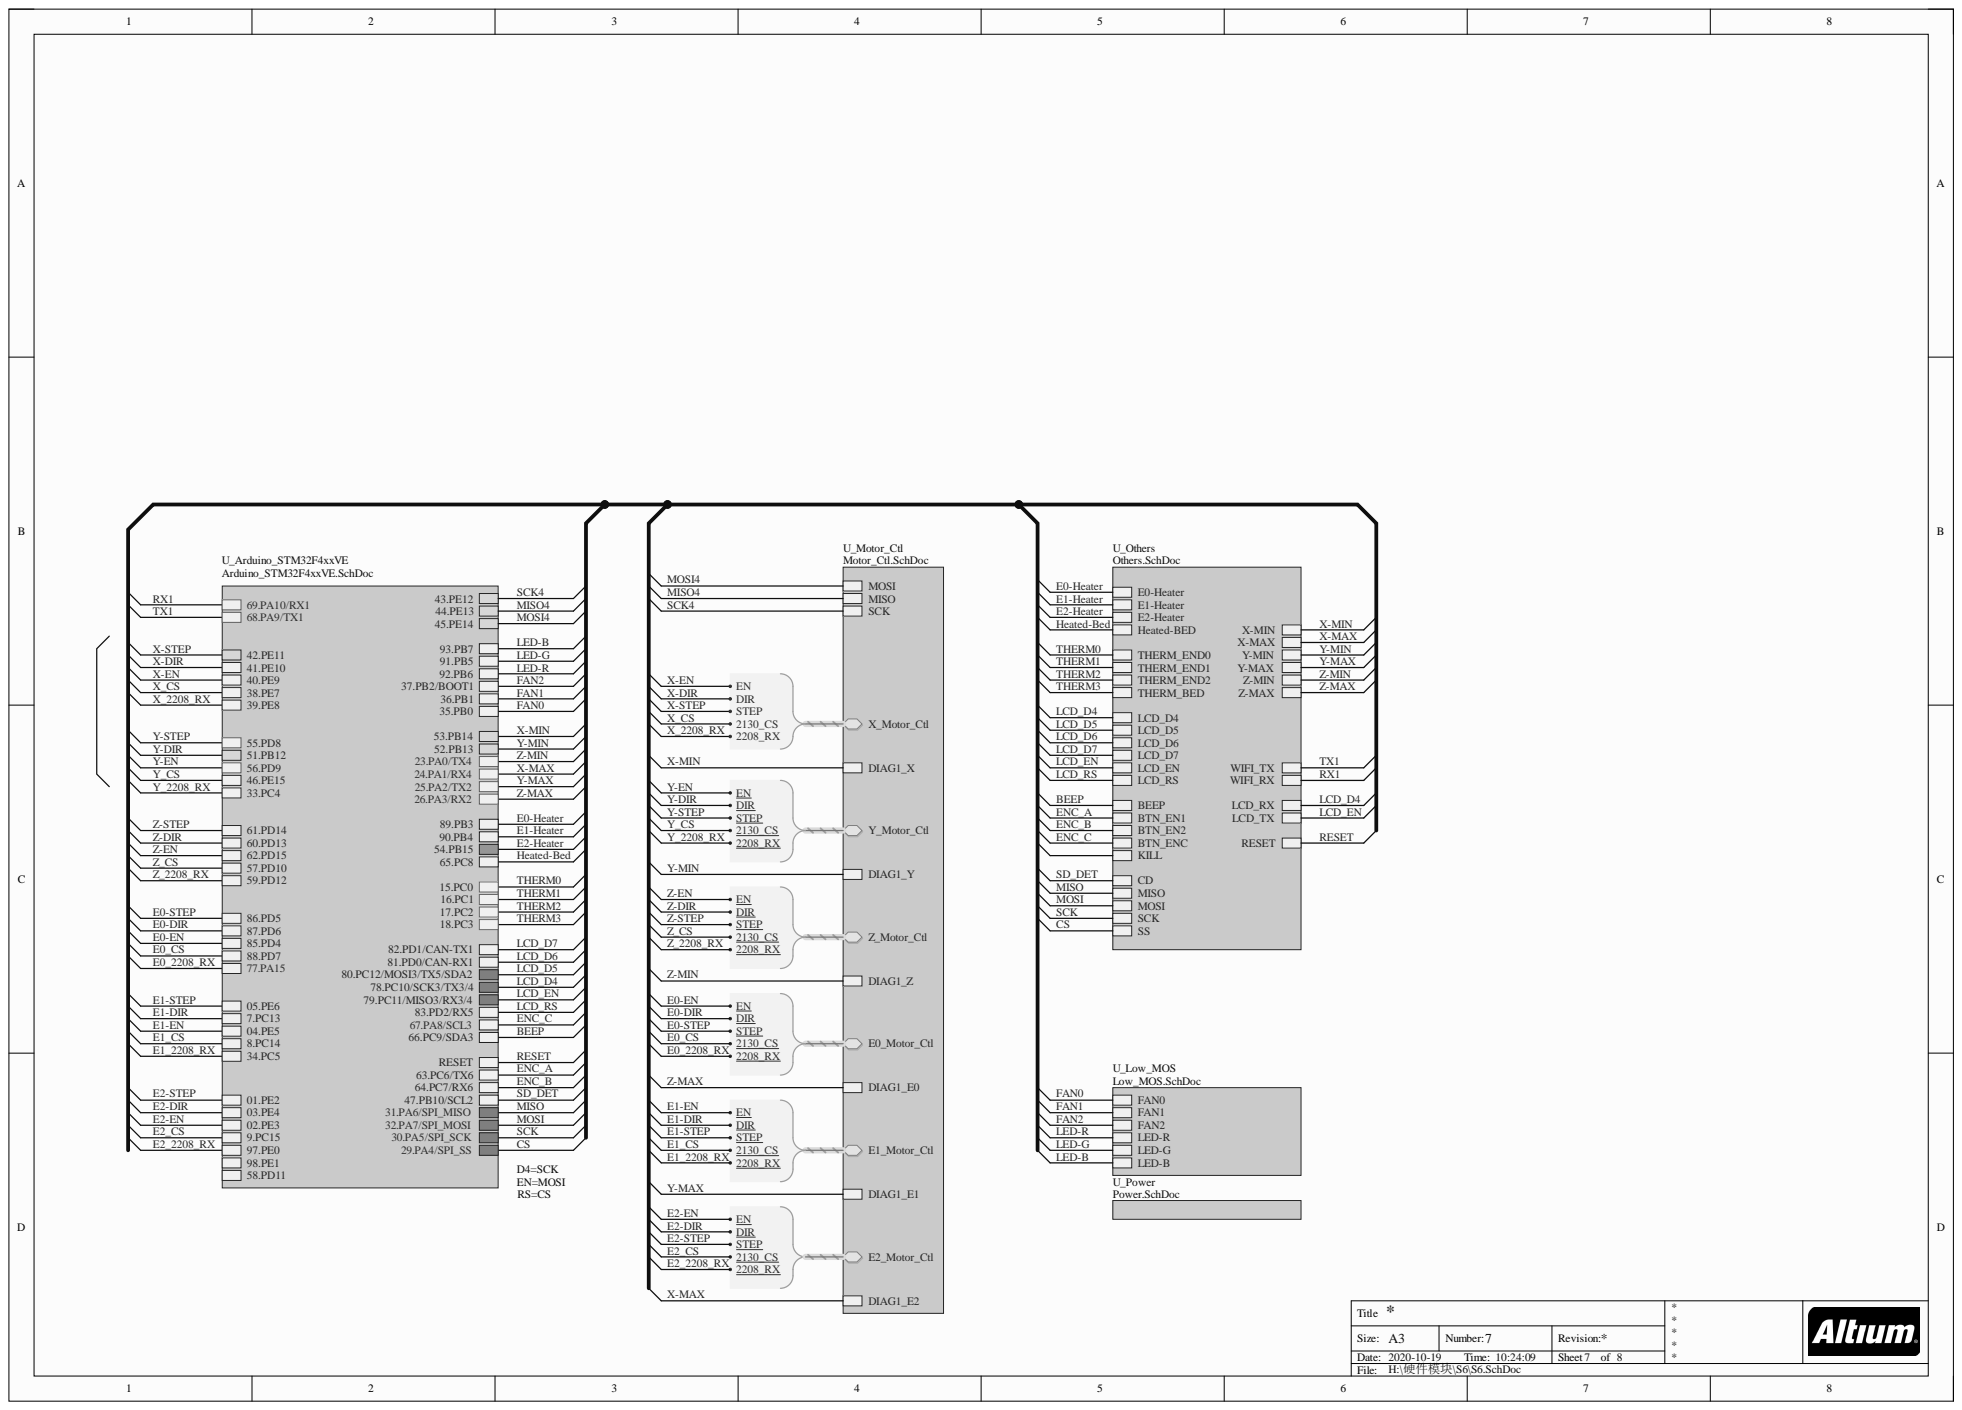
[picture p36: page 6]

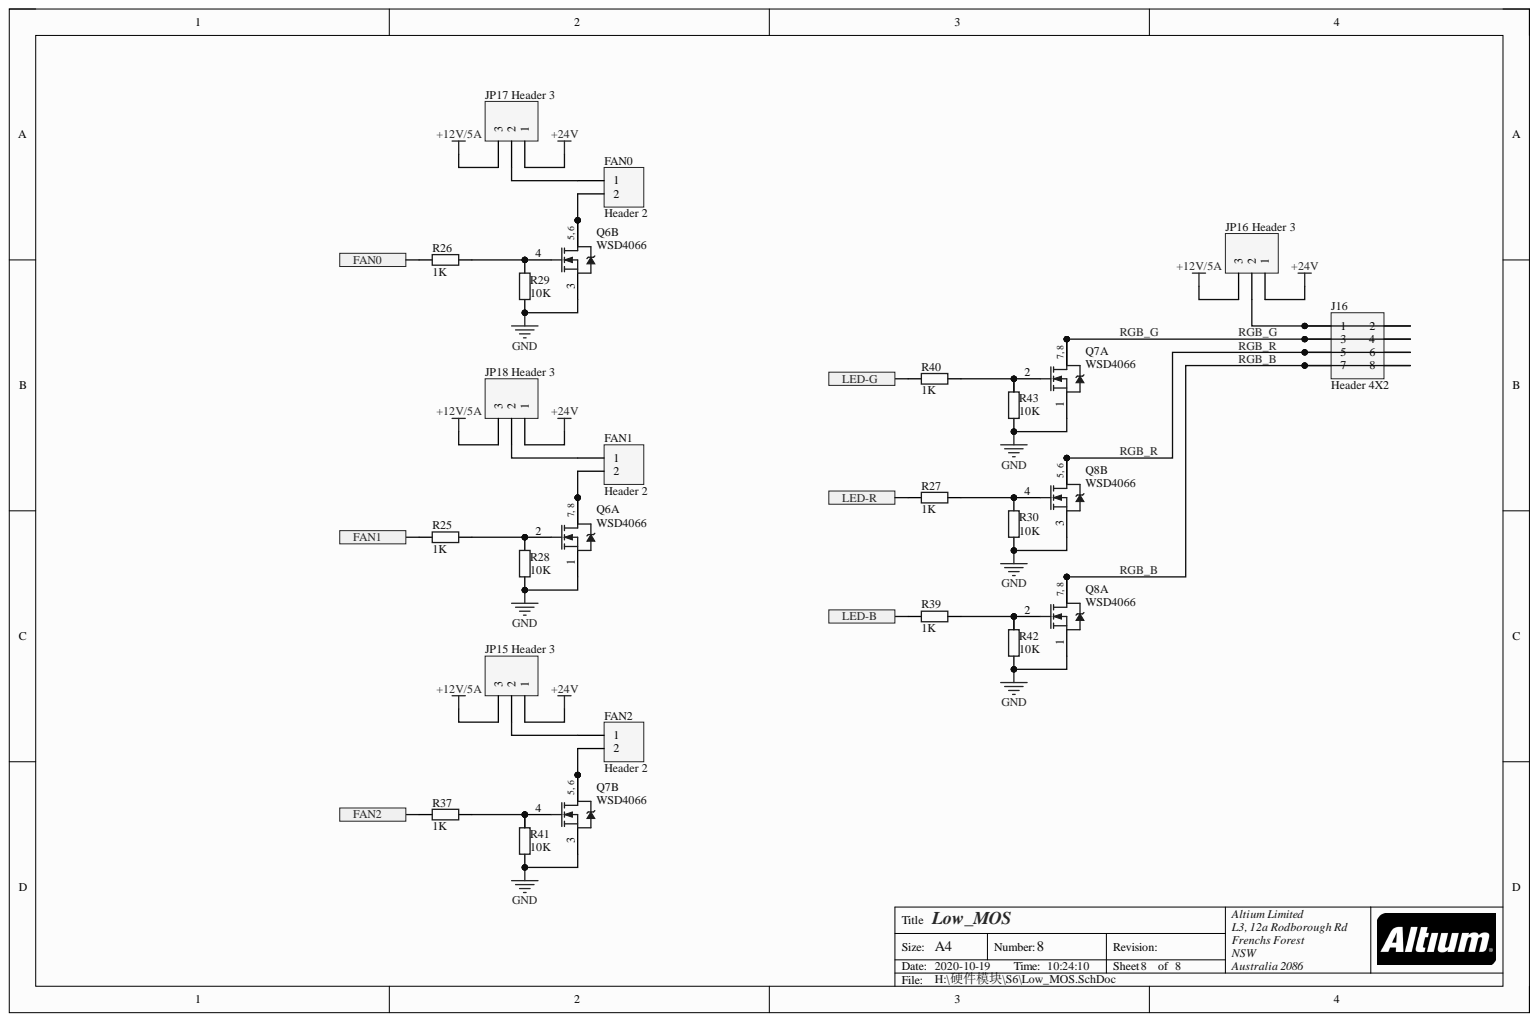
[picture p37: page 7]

RGB_ R Q 7 A | 5 6

RGB_ B | 7 8

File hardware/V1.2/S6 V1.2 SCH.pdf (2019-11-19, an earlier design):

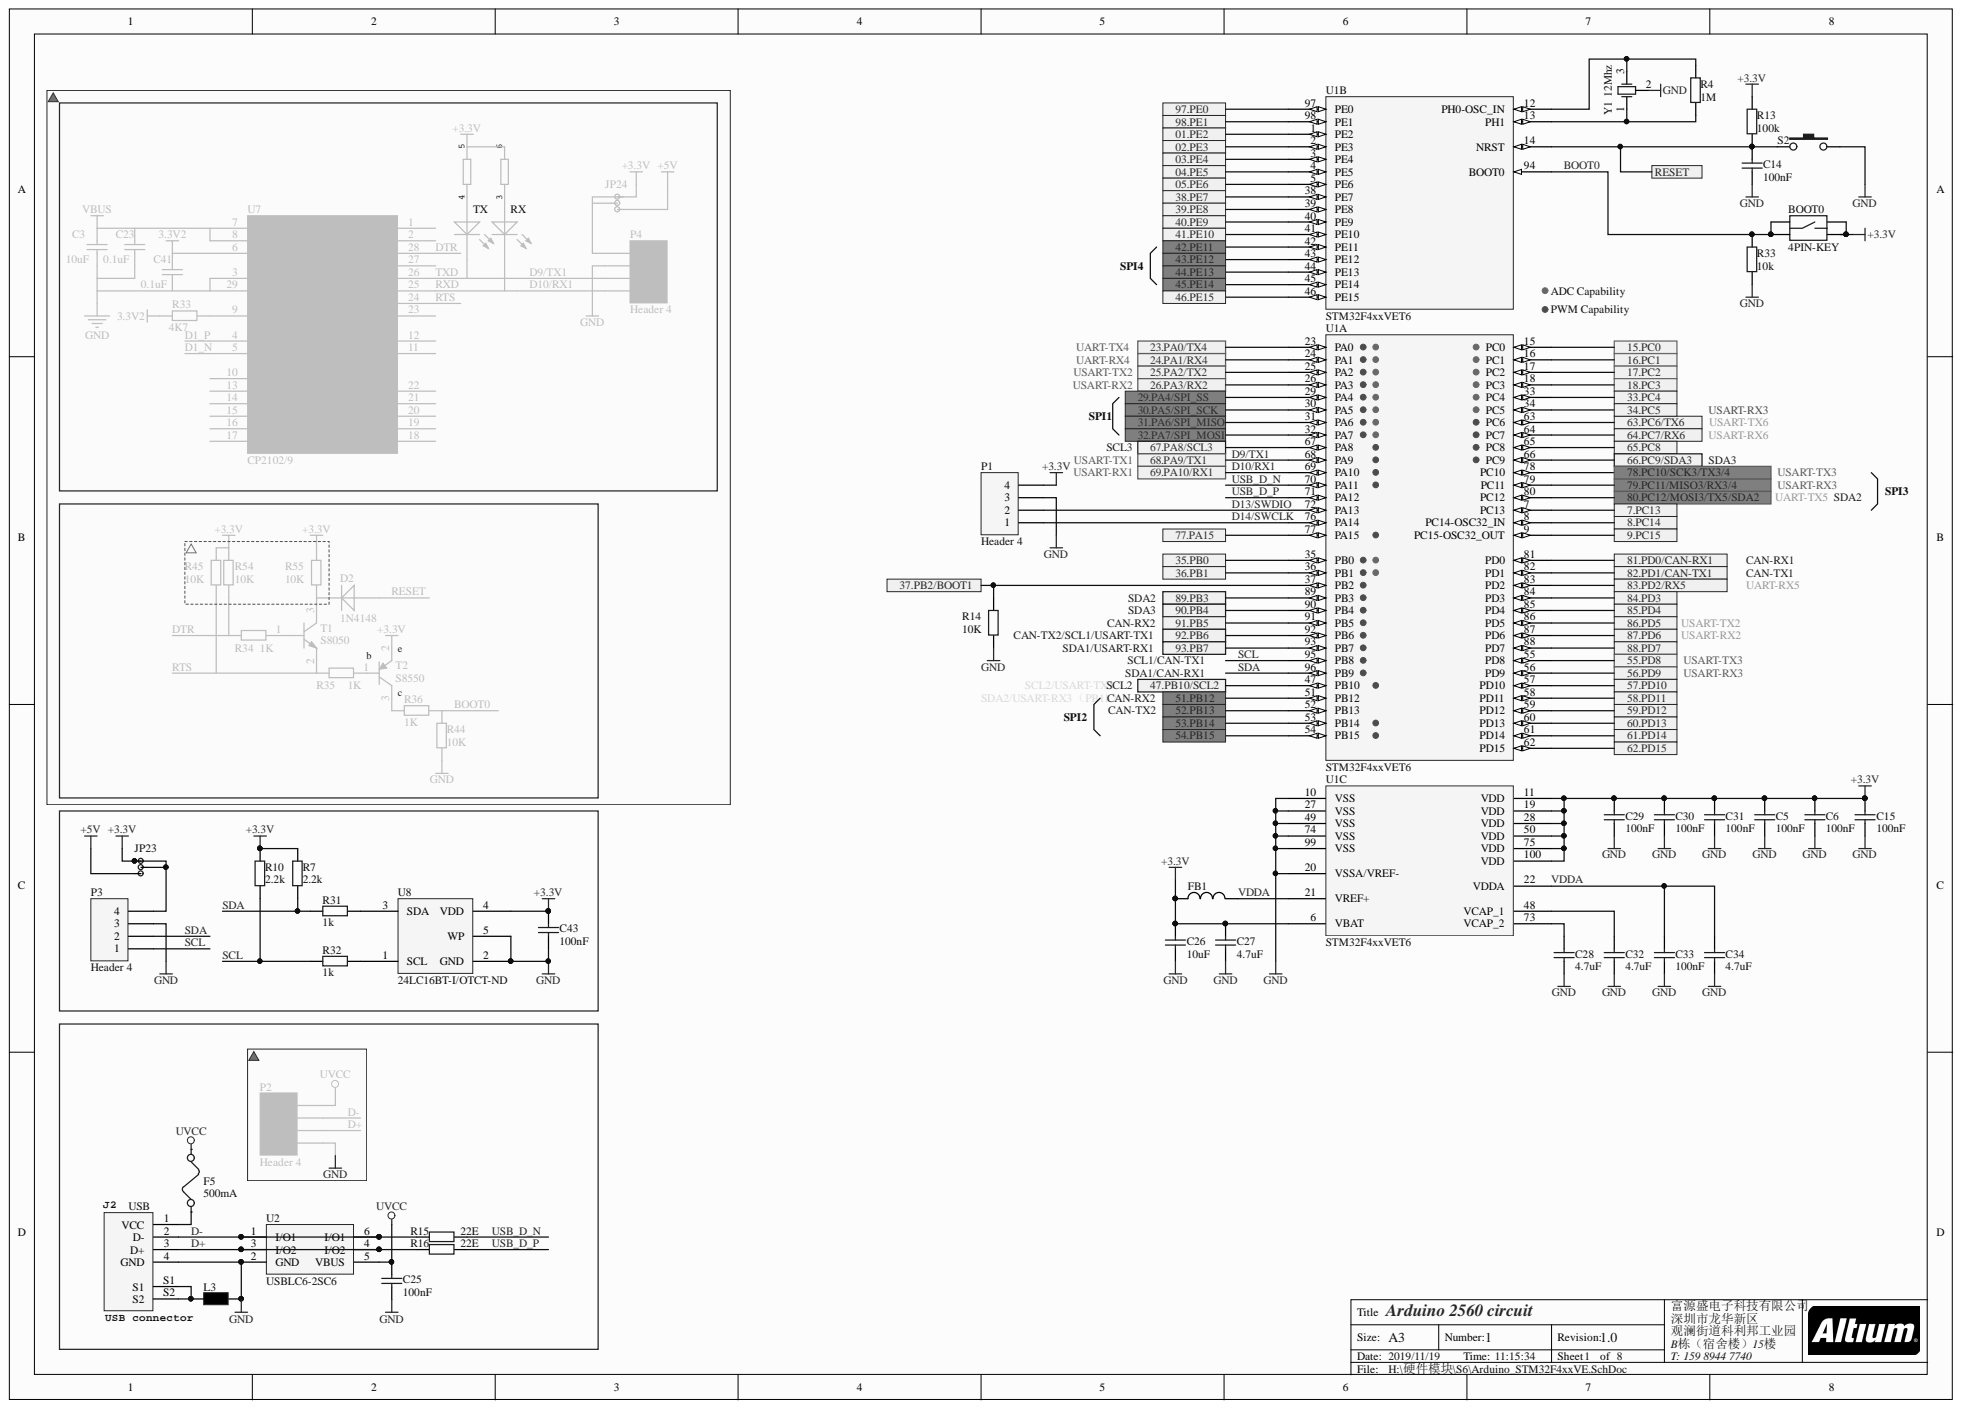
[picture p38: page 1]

98.PE1 | PE1 98
01.PE2 | PE3 2
03.PE4 | PE4 3 | BOOT0
04.PE5 | PE6 5 | | RESET

32.PA7/SPI_MOSI | | PA7 32 | 64.PC7/RX6
67.PA8/SCL3 | D9/TX1 | PA9 68 | 65.PC8

D14/SWCLK | PA14 76 | | 8.PC14

36.PB1 | | PB1 36 | | 82.PD1/CAN-TX1

37.PB2/BOOT1 | | | | PB3 89 | | 83.PD2/RX5

89.PB3 | | PB4 90 | | 84.PD3
91.PB5 | PB5 91 | 86.PD5
92.PB6 | PB7 93 | 87.PD6
93.PB7 | | 88.PD7

47.PB10/SCL2 | PB12 51 | 57.PD10
51.PB12 | | 58.PD11
52.PB13 | PB13 52 | 59.PD12
53.PB14 | PB15 54 | 60.PD13
54.PB15 | | 61.PD14

Arduino 2560 circuit Title | 富源盛电子科技有限公司 深圳市龙华新区 观澜街道科利邦工业园 B栋（宿舍楼）15楼 T: 159 8944 7740

Size: A3 | Number: 1 | Revision: 1.0
Date: 2019/11/19 Time: 11:15:34 | | Sheet of 8

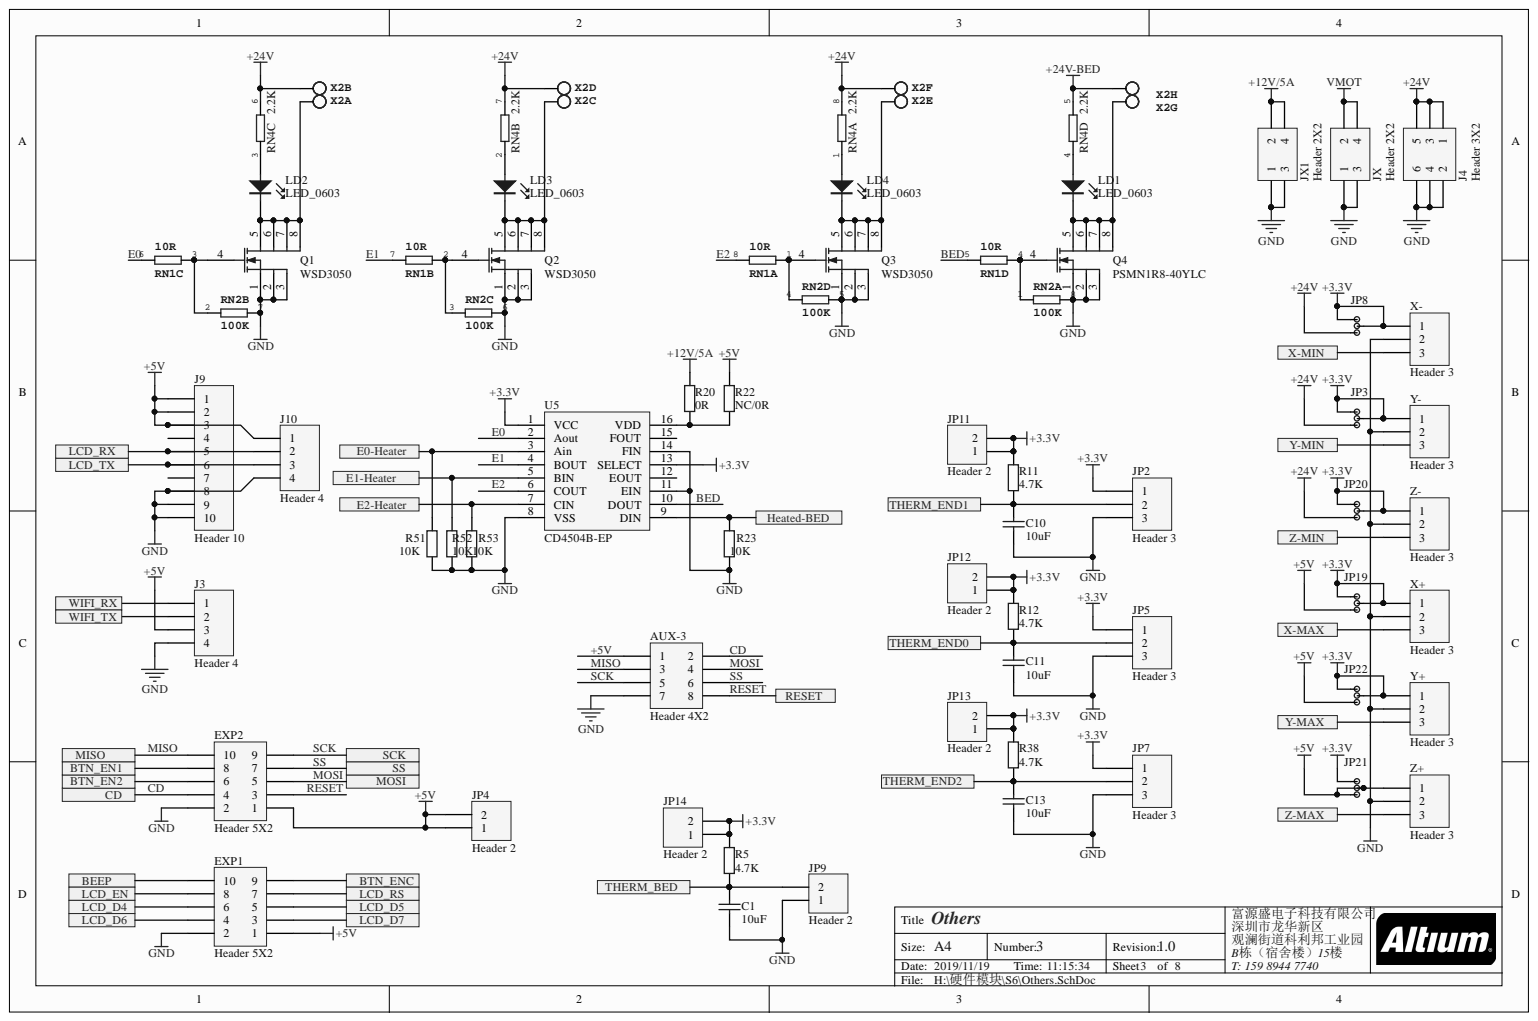
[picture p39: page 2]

LCD_EN | LCD_RS

Others Title | 富源盛电子科技有限公司 深圳市龙华新区 观澜街道科利邦工业园 T: 159 8944 7740

Size: A4 | Number: 3 | Revision: 1.0 | B栋（宿舍楼）15楼 8
2019/11/19 Time: 11:15:34 | | Sheet of


Power Title | 富源盛电子科技有限公司 深圳市龙华新区 观澜街道科利邦工业园 T: 159 8944 7740

Size: A4 | Number: 4 | Revision: 1.0 | B栋（宿舍楼）15楼 8
2019/11/19 Time: 11:15:34 | | Sheet of


2 MS2 SC K | 3 | 1 4
3 MS3 C S | 4 | 1 3 | | 2 A
4 CFG 0 ISO M | 5 | 1 2 | | 1 A

Motor_Driver T i t l e | 富源盛电子科技有限公司 深圳市龙华新区 观澜街道科利邦工业园 B栋（宿舍楼）15楼 T: 1 9 8 4 7

Size: A4 | N umber: 5 | Rev i s i o n : 1.0

/ / T ime: : | | Sheet o f


Motor_Ctl T i t l e | A l t i u m Li m i ted L3, 1 2 a R o d b o ro u g h R d F rench s F o res t NS W A u s t r a l i a 2

Size: A4 | N umber: 6 | Rev i s i o n :

/ / T ime: | | Sheet o f


D53 E1-Heater Heated-Bed E0-Heater

Size: A | Number | Revi s ion: *
2019/ 11/19 Ti me: 11:15:34 | | Sheet of


RGB_ R Q 7 A | 5 6

RGB_ B | 7 8

Low_MO S T i t l e | A l t i u m Li m i ted L3, 1 2 a R o d b o ro u g h R d F rench s F o res t NS W A u s t r a l i a 2

Size: A4 | N umber: 8 | Rev i s i o n :

/ / T ime: | | Sheet o f



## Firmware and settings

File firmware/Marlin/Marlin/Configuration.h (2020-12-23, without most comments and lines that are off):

#pragma once
#define CONFIGURATION_H_VERSION 020007
#define STRING_CONFIG_H_AUTHOR "(none, default config)" // Who made the changes.
#define SHOW_BOOTSCREEN
#define SERIAL_PORT -1
#define BAUDRATE 115200
  #define MOTHERBOARD BOARD_FYSETC_S6_V2_0
#define EXTRUDERS 1
#define DEFAULT_NOMINAL_FILAMENT_DIA 1.75
#define TEMP_SENSOR_0 1
#define TEMP_SENSOR_1 0
#define TEMP_SENSOR_2 0
#define TEMP_SENSOR_3 0
#define TEMP_SENSOR_4 0
#define TEMP_SENSOR_5 0
#define TEMP_SENSOR_6 0
#define TEMP_SENSOR_7 0
#define TEMP_SENSOR_BED 0
#define TEMP_SENSOR_PROBE 0
#define TEMP_SENSOR_CHAMBER 0
#define DUMMY_THERMISTOR_998_VALUE 25
#define DUMMY_THERMISTOR_999_VALUE 100
#define MAX_REDUNDANT_TEMP_SENSOR_DIFF 10
#define TEMP_RESIDENCY_TIME     10  // (seconds) Time to wait for hotend to "settle" in M109
#define TEMP_WINDOW              1  // (°C) Temperature proximity for the "temperature reached" timer
#define TEMP_HYSTERESIS          3  // (°C) Temperature proximity considered "close enough" to the target
#define TEMP_BED_RESIDENCY_TIME 10  // (seconds) Time to wait for bed to "settle" in M190
#define TEMP_BED_WINDOW          1  // (°C) Temperature proximity for the "temperature reached" timer
#define TEMP_BED_HYSTERESIS      3  // (°C) Temperature proximity considered "close enough" to the target
#define HEATER_0_MINTEMP   5
#define HEATER_1_MINTEMP   5
#define HEATER_2_MINTEMP   5
#define HEATER_3_MINTEMP   5
#define HEATER_4_MINTEMP   5
#define HEATER_5_MINTEMP   5
#define HEATER_6_MINTEMP   5
#define HEATER_7_MINTEMP   5
#define BED_MINTEMP        5
#define HEATER_0_MAXTEMP 275
#define HEATER_1_MAXTEMP 275
#define HEATER_2_MAXTEMP 275
#define HEATER_3_MAXTEMP 275
#define HEATER_4_MAXTEMP 275
#define HEATER_5_MAXTEMP 275
#define HEATER_6_MAXTEMP 275
#define HEATER_7_MAXTEMP 275
#define BED_MAXTEMP      150
#define PIDTEMP
#define BANG_MAX 255     // Limits current to nozzle while in bang-bang mode; 255=full current
#define PID_MAX BANG_MAX // Limits current to nozzle while PID is active (see PID_FUNCTIONAL_RANGE below); 255=full current
#define PID_K1 0.95      // Smoothing factor within any PID loop
    #define DEFAULT_Kp  22.20
    #define DEFAULT_Ki   1.08
    #define DEFAULT_Kd 114.00
#define MAX_BED_POWER 255 // limits duty cycle to bed; 255=full current
  #define PID_FUNCTIONAL_RANGE 10 // If the temperature difference between the target temperature and the actual temperature
#define PREVENT_COLD_EXTRUSION
#define EXTRUDE_MINTEMP 170
#define PREVENT_LENGTHY_EXTRUDE
#define EXTRUDE_MAXLENGTH 200
#define THERMAL_PROTECTION_HOTENDS // Enable thermal protection for all extruders
#define THERMAL_PROTECTION_BED     // Enable thermal protection for the heated bed
#define THERMAL_PROTECTION_CHAMBER // Enable thermal protection for the heated chamber
#define USE_XMIN_PLUG
#define USE_YMIN_PLUG
#define USE_ZMIN_PLUG
#define ENDSTOPPULLUPS
#define X_MIN_ENDSTOP_INVERTING false // Set to true to invert the logic of the endstop.
#define Y_MIN_ENDSTOP_INVERTING false // Set to true to invert the logic of the endstop.
#define Z_MIN_ENDSTOP_INVERTING false // Set to true to invert the logic of the endstop.
#define X_MAX_ENDSTOP_INVERTING false // Set to true to invert the logic of the endstop.
#define Y_MAX_ENDSTOP_INVERTING false // Set to true to invert the logic of the endstop.
#define Z_MAX_ENDSTOP_INVERTING false // Set to true to invert the logic of the endstop.
#define Z_MIN_PROBE_ENDSTOP_INVERTING false // Set to true to invert the logic of the probe.
#define DEFAULT_AXIS_STEPS_PER_UNIT   { 80, 80, 4000, 500 }
#define DEFAULT_MAX_FEEDRATE          { 300, 300, 5, 25 }
#define DEFAULT_MAX_ACCELERATION      { 3000, 3000, 100, 10000 }
#define DEFAULT_ACCELERATION          3000    // X, Y, Z and E acceleration for printing moves
#define DEFAULT_RETRACT_ACCELERATION  3000    // E acceleration for retracts
#define DEFAULT_TRAVEL_ACCELERATION   3000    // X, Y, Z acceleration for travel (non printing) moves
#define DEFAULT_EJERK    5.0  // May be used by Linear Advance
  #define JUNCTION_DEVIATION_MM 0.013 // (mm) Distance from real junction edge
  #define JD_HANDLE_SMALL_SEGMENTS    // Use curvature estimation instead of just the junction angle
#define Z_MIN_PROBE_USES_Z_MIN_ENDSTOP_PIN
#define NOZZLE_TO_PROBE_OFFSET { 10, 10, 0 }
#define PROBING_MARGIN 10
#define XY_PROBE_SPEED (133*60)
#define Z_PROBE_SPEED_FAST HOMING_FEEDRATE_Z
#define Z_PROBE_SPEED_SLOW (Z_PROBE_SPEED_FAST / 2)
#define Z_CLEARANCE_DEPLOY_PROBE   10 // Z Clearance for Deploy/Stow
#define Z_CLEARANCE_BETWEEN_PROBES  5 // Z Clearance between probe points
#define Z_CLEARANCE_MULTI_PROBE     5 // Z Clearance between multiple probes
#define Z_PROBE_LOW_POINT          -2 // Farthest distance below the trigger-point to go before stopping
#define Z_PROBE_OFFSET_RANGE_MIN -20
#define Z_PROBE_OFFSET_RANGE_MAX 20
#define X_ENABLE_ON 0
#define Y_ENABLE_ON 0
#define Z_ENABLE_ON 0
#define E_ENABLE_ON 0 // For all extruders
#define DISABLE_X false
#define DISABLE_Y false
#define DISABLE_Z false
#define DISABLE_E false             // Disable the extruder when not stepping
#define DISABLE_INACTIVE_EXTRUDER   // Keep only the active extruder enabled
#define INVERT_X_DIR false
#define INVERT_Y_DIR true
#define INVERT_Z_DIR false
#define INVERT_E0_DIR false
#define INVERT_E1_DIR false
#define INVERT_E2_DIR false
#define INVERT_E3_DIR false
#define INVERT_E4_DIR false
#define INVERT_E5_DIR false
#define INVERT_E6_DIR false
#define INVERT_E7_DIR false
#define X_HOME_DIR -1
#define Y_HOME_DIR -1
#define Z_HOME_DIR -1
#define X_BED_SIZE 200
#define Y_BED_SIZE 200
#define X_MIN_POS 0
#define Y_MIN_POS 0
#define Z_MIN_POS 0
#define X_MAX_POS X_BED_SIZE
#define Y_MAX_POS Y_BED_SIZE
#define Z_MAX_POS 200
#define MIN_SOFTWARE_ENDSTOPS
  #define MIN_SOFTWARE_ENDSTOP_X
  #define MIN_SOFTWARE_ENDSTOP_Y
  #define MIN_SOFTWARE_ENDSTOP_Z
#define MAX_SOFTWARE_ENDSTOPS
  #define MAX_SOFTWARE_ENDSTOP_X
  #define MAX_SOFTWARE_ENDSTOP_Y
  #define MAX_SOFTWARE_ENDSTOP_Z
#define HOMING_FEEDRATE_XY (50*60)
#define HOMING_FEEDRATE_Z  (4*60)
#define VALIDATE_HOMING_ENDSTOPS
#define EEPROM_SETTINGS     // Persistent storage with M500 and M501
#define EEPROM_CHITCHAT       // Give feedback on EEPROM commands. Disable to save PROGMEM.
#define EEPROM_BOOT_SILENT    // Keep M503 quiet and only give errors during first load
#define HOST_KEEPALIVE_FEATURE        // Disable this if your host doesn't like keepalive messages
#define DEFAULT_KEEPALIVE_INTERVAL 2  // Number of seconds between "busy" messages. Set with M113.
#define BUSY_WHILE_HEATING            // Some hosts require "busy" messages even during heating
#define PREHEAT_1_LABEL       "PLA"
#define PREHEAT_1_TEMP_HOTEND 180
#define PREHEAT_1_TEMP_BED     70
#define PREHEAT_1_FAN_SPEED     0 // Value from 0 to 255
#define PREHEAT_2_LABEL       "ABS"
#define PREHEAT_2_TEMP_HOTEND 240
#define PREHEAT_2_TEMP_BED    110
#define PREHEAT_2_FAN_SPEED     0 // Value from 0 to 255
#define PRINTJOB_TIMER_AUTOSTART
#define LCD_LANGUAGE en
#define DISPLAY_CHARSET_HD44780 JAPANESE
#define LCD_INFO_SCREEN_STYLE 0
#define SDSUPPORT
#define TOUCH_UI_FTDI_EVE
#define SOFT_PWM_SCALE 0
#define SERVO_DELAY { 300 }

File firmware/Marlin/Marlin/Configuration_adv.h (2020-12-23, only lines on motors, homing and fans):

#define E0_AUTO_FAN_PIN -1
#define E1_AUTO_FAN_PIN -1
#define E2_AUTO_FAN_PIN -1
#define E3_AUTO_FAN_PIN -1
#define E4_AUTO_FAN_PIN -1
#define E5_AUTO_FAN_PIN -1
#define E6_AUTO_FAN_PIN -1
#define E7_AUTO_FAN_PIN -1
#define CHAMBER_AUTO_FAN_PIN -1
#define HOMING_BUMP_MM      { 5, 5, 2 }       // (mm) Backoff from endstops after first bump
#define HOMING_BUMP_DIVISOR { 2, 2, 4 }       // Re-Bump Speed Divisor (Divides the Homing Feedrate)
#define MICROSTEP_MODES { 16, 16, 16, 16, 16, 16 } // [1,2,4,8,16]

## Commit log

2020-10-19 Upload 2.0
    [Arduino_STM32F4xxVE.SchDoc, Low_MOS.SchDoc, Motor_Ctl.SchDoc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]
2020-12-03 Rearrange docs structure
    [Arduino_STM32F4xxVE.SchDoc, Low_MOS.SchDoc, Motor_Ctl.SchDoc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]
2020-12-23 Upload Marlin 2.7.2
    [Configuration.h, Configuration_adv.h]
2021-05-31 Update README for TMC2209 wiring
2021-12-20 Update FYSETC S6 pin def

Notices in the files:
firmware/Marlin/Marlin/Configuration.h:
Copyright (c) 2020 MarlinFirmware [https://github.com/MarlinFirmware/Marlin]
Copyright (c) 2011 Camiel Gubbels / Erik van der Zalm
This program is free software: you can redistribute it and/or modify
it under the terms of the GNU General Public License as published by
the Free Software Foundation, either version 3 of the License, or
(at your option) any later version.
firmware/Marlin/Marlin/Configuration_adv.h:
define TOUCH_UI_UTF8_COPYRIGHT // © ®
